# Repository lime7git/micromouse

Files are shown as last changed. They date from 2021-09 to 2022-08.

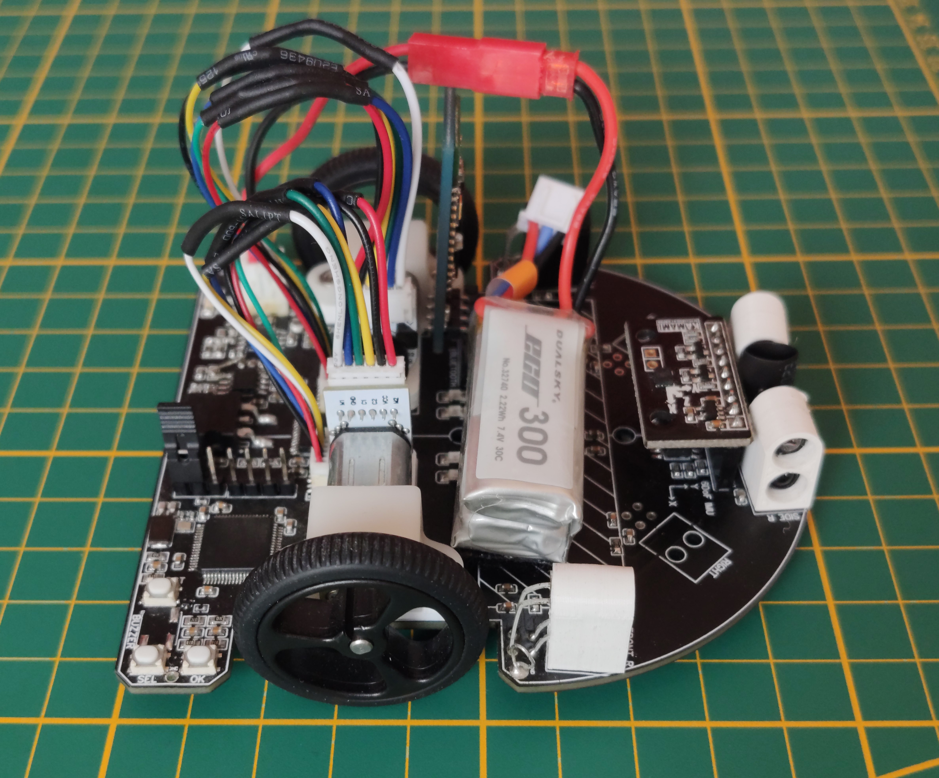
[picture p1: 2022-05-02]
micromouse-hardware/image8.jpg

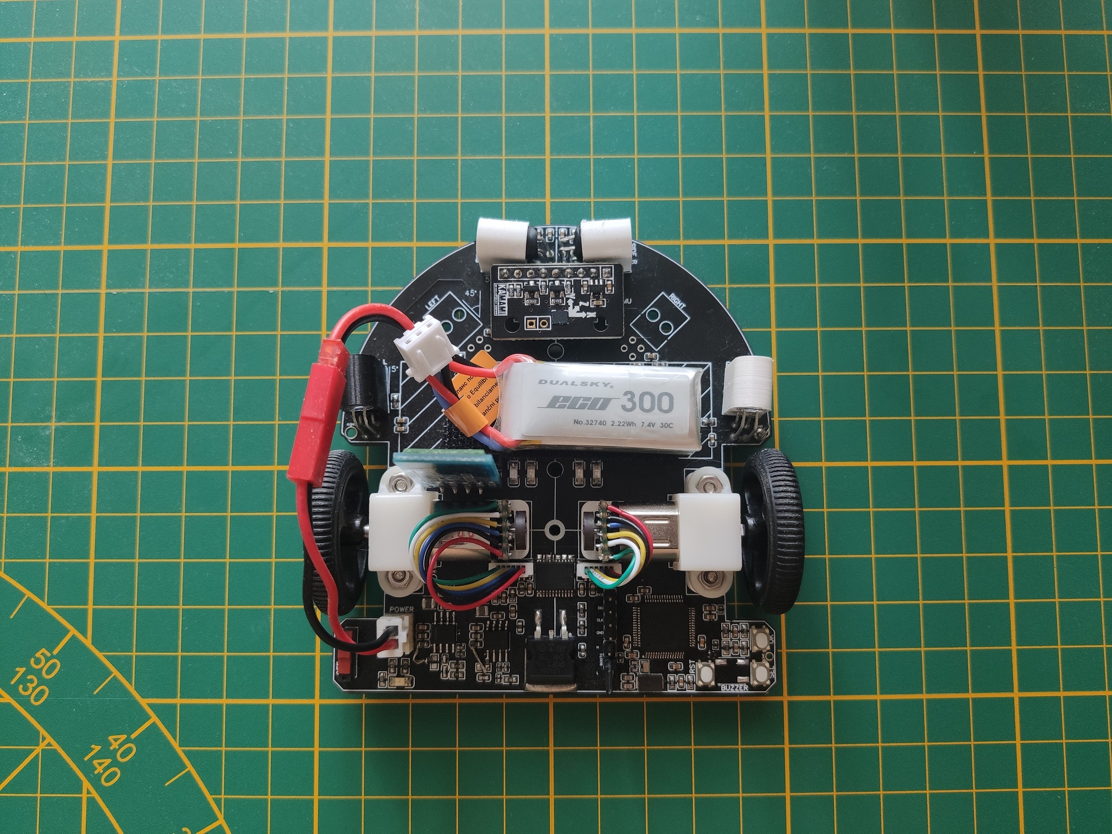
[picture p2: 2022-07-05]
micromouse-hardware/image12.jpg

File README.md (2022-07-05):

# micromouse

Project of a micromouse type mobile robot based on STM32 and designed PCB used as a chasis. It is my Master's Degree thesis at The Kielce University of Technology.

Project involve robot hardware and software design, build a small maze where robot will be tested and program a maze simulator windows application to test and compare different maze search alghoritms. The simulator is created with Qt 6 libary and Qt Creator IDE. Hardware design was created with EasyEDA. Robot's software was written in C programming language in Keil uVision5 IDE.




Maze simulator (https://youtu.be/YN4h0kgOSEQ "Micromouse")

Micromouse (https://www.youtube.com/watch?v=JYLGGba1-mw "Micromouse")

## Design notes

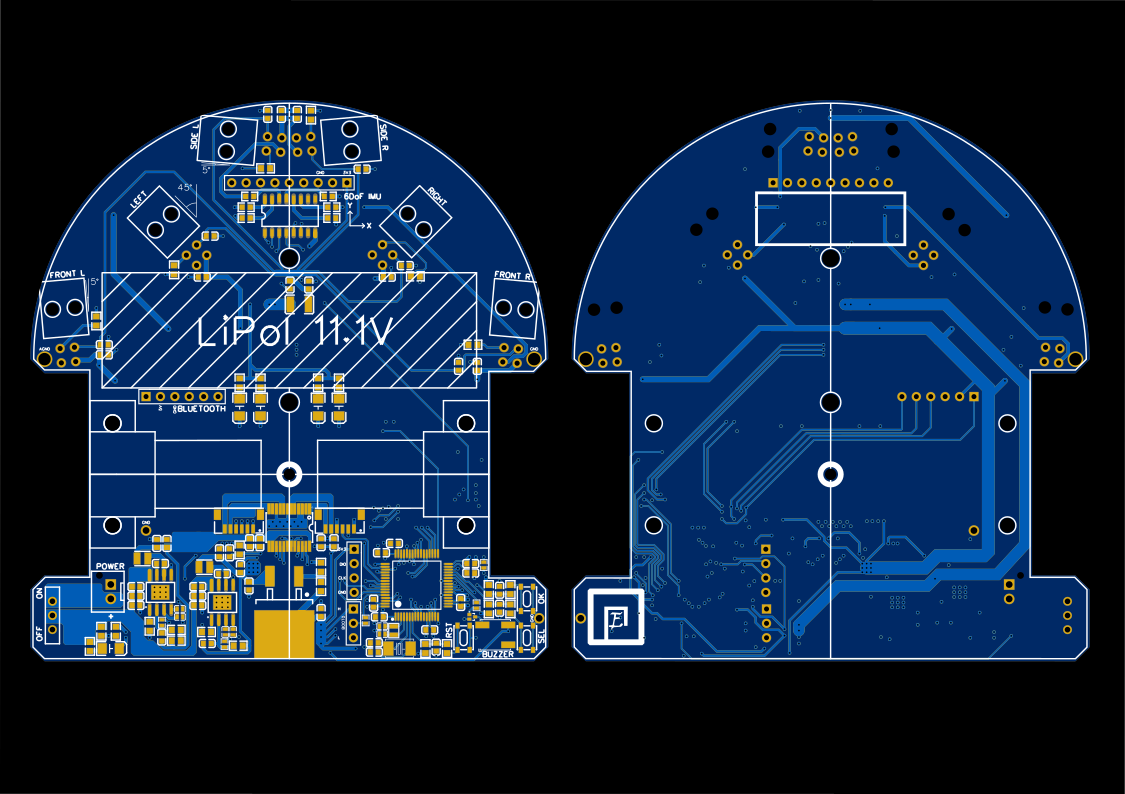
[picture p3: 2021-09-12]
micromouse-hardware/pcb-preview.png

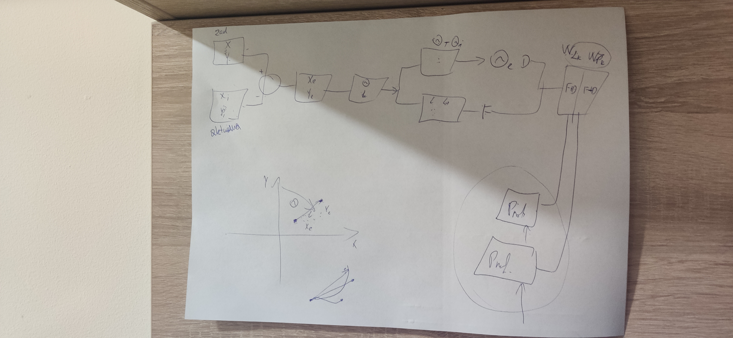
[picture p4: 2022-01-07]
micromouse-docs/position-speed-control-diagram.jpg

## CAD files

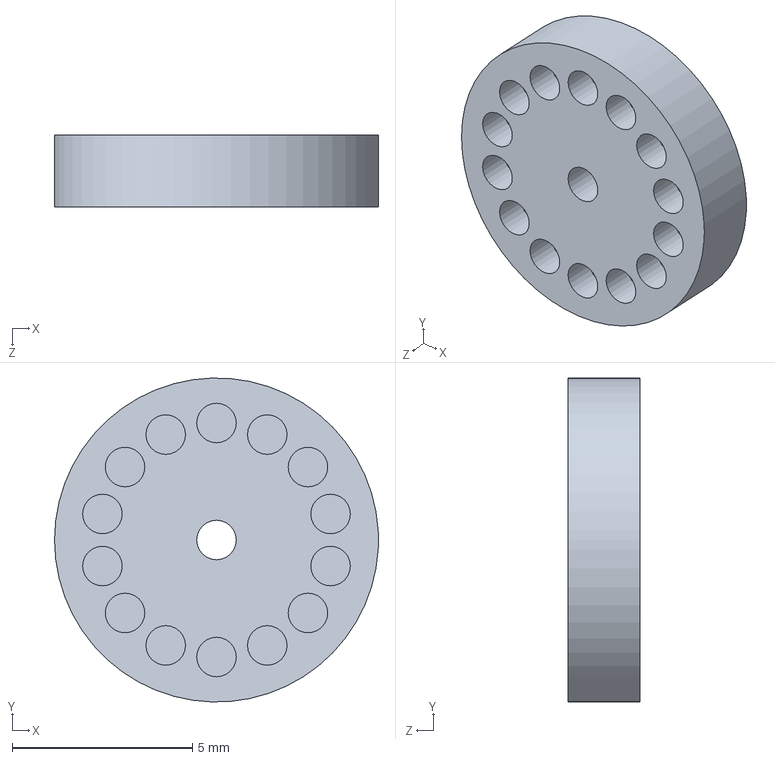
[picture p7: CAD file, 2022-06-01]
micromouse-other/encoder-magnet-disc-3d/14-pole-encoder-disk-2mm-height.SLDPRT
9.00 x 9.00 x 2.00 mm

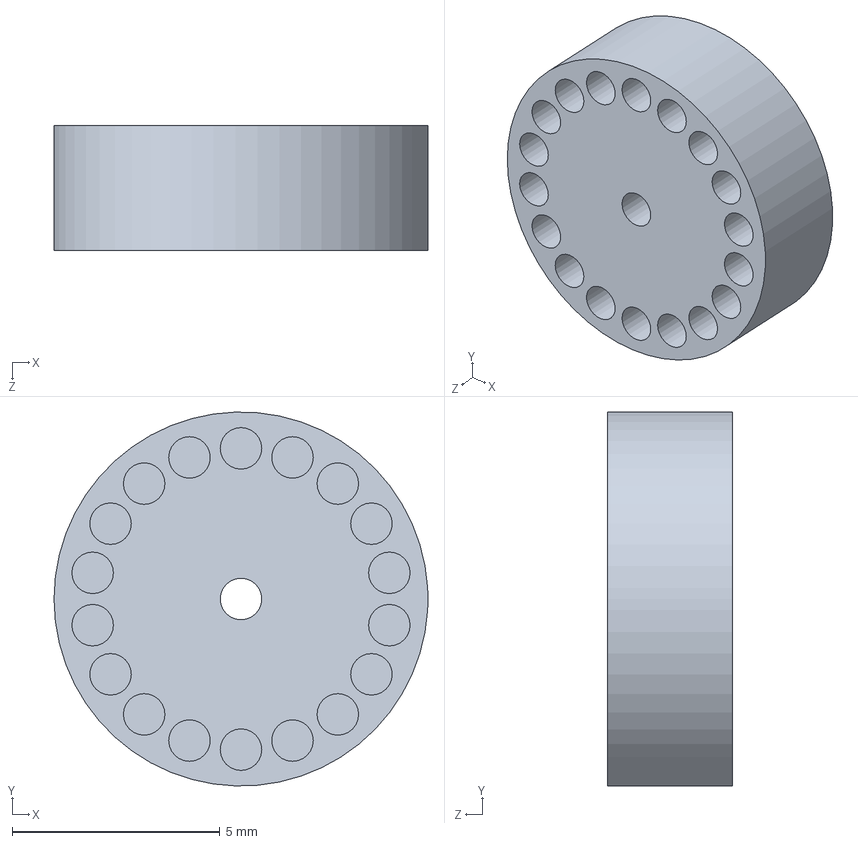
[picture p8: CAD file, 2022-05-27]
micromouse-other/encoder-magnet-disc-3d/18-pole-encoder-disk.SLDPRT
9.00 x 9.00 x 3.00 mm

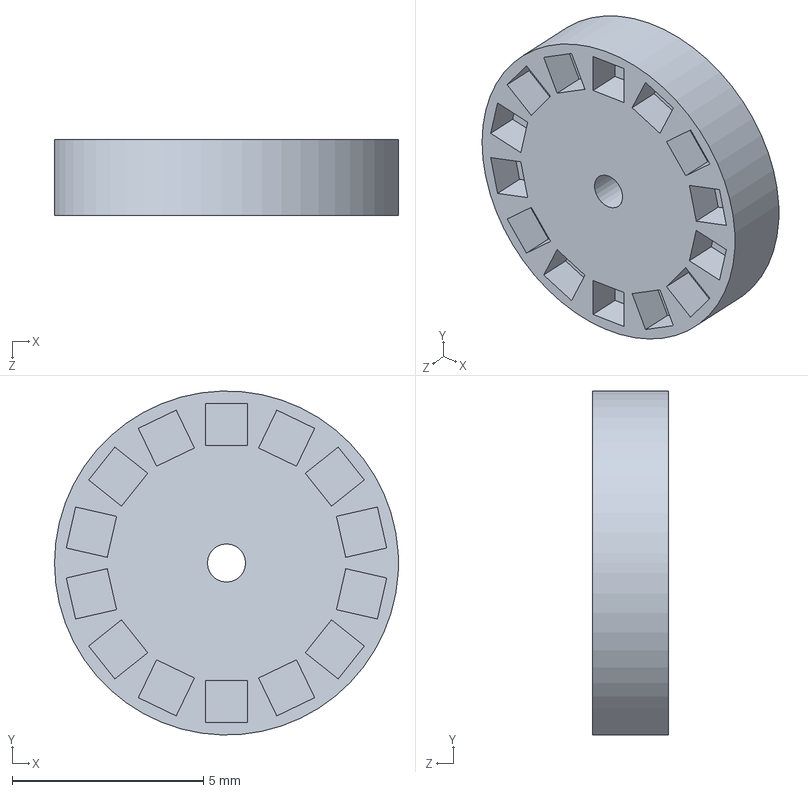
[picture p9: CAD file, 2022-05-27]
micromouse-other/encoder-magnet-disc-3d/14-pole-encoder-disk-2mm-height-square-holes.SLDPRT
9.00 x 9.00 x 2.00 mm

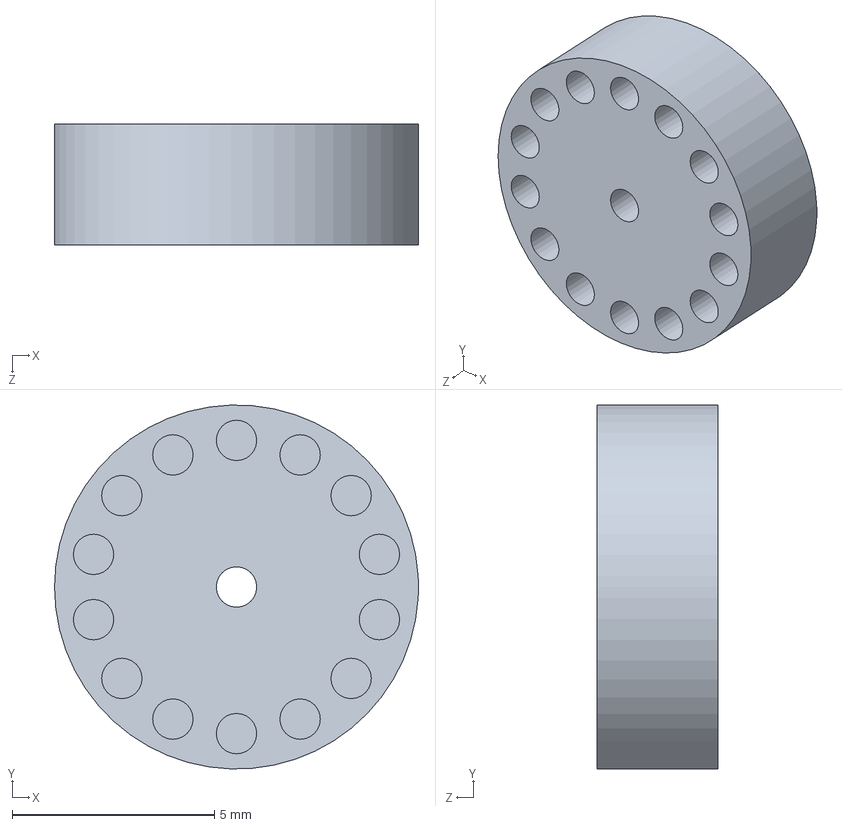
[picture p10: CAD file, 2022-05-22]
micromouse-other/encoder-magnet-disc-3d/14-pole-encoder-disk.SLDPRT
9.00 x 9.00 x 3.00 mm

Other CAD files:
micromouse-other/encoder-magnet-disc-3d/18-pole-encoder-disk-2mm-height.SLDPRT
micromouse-other/encoder-magnet-disc-3d/14-pole-encoder-disk-2mm-height-square-holes.STL
micromouse-other/encoder-magnet-disc-3d/14-pole-encoder-disk-2mm-height.STL
micromouse-other/encoder-magnet-disc-3d/14-pole-encoder-disk.STL
micromouse-other/encoder-magnet-disc-3d/18-pole-encoder-disk-2mm-height.STL
micromouse-other/encoder-magnet-disc-3d/18-pole-encoder-disk.STL

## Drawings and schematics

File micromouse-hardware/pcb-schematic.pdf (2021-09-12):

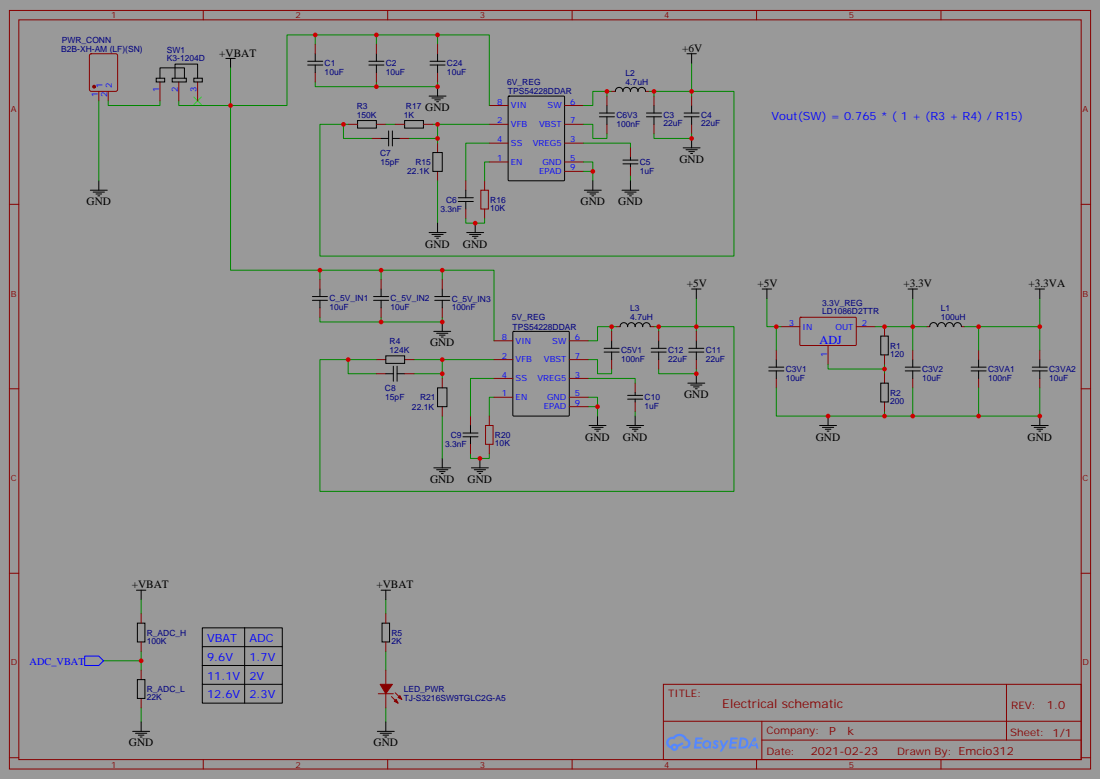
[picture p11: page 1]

PWR_CONN

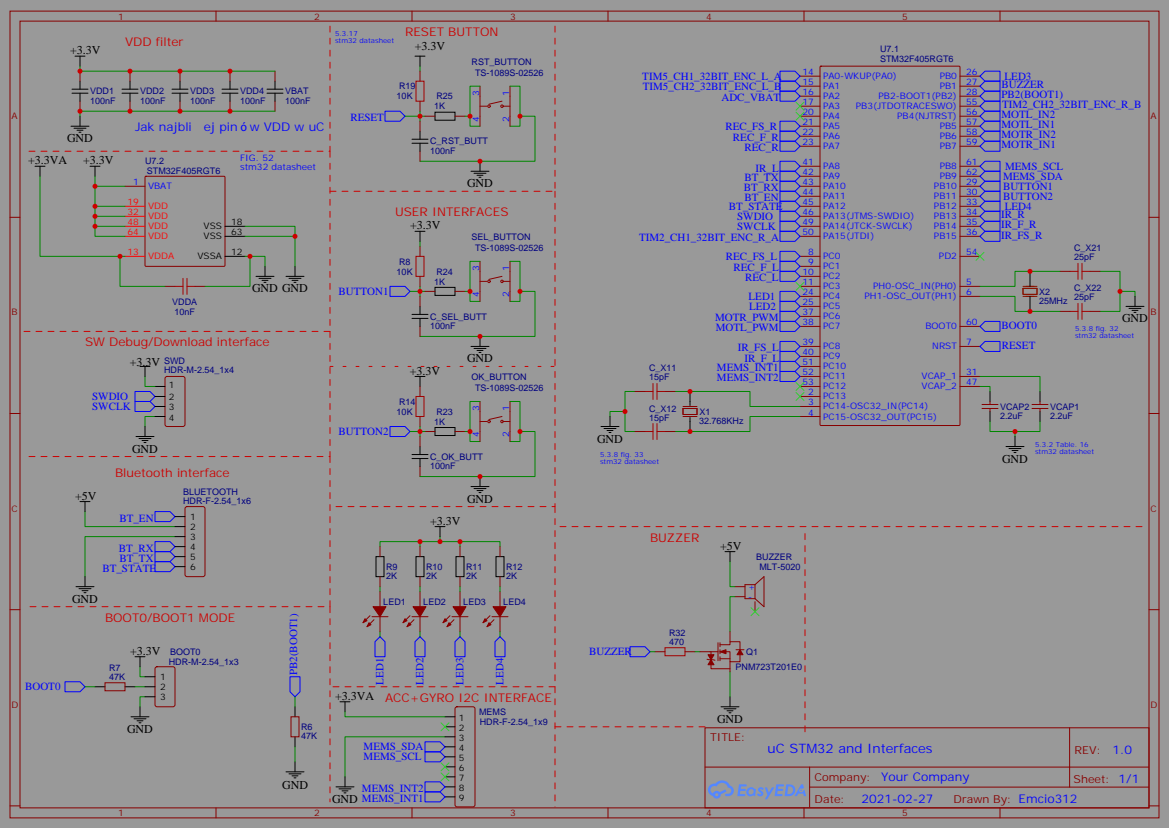
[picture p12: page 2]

VDD2
Jak najbli ej pin w VDD w uC

SW Debug/Download interface

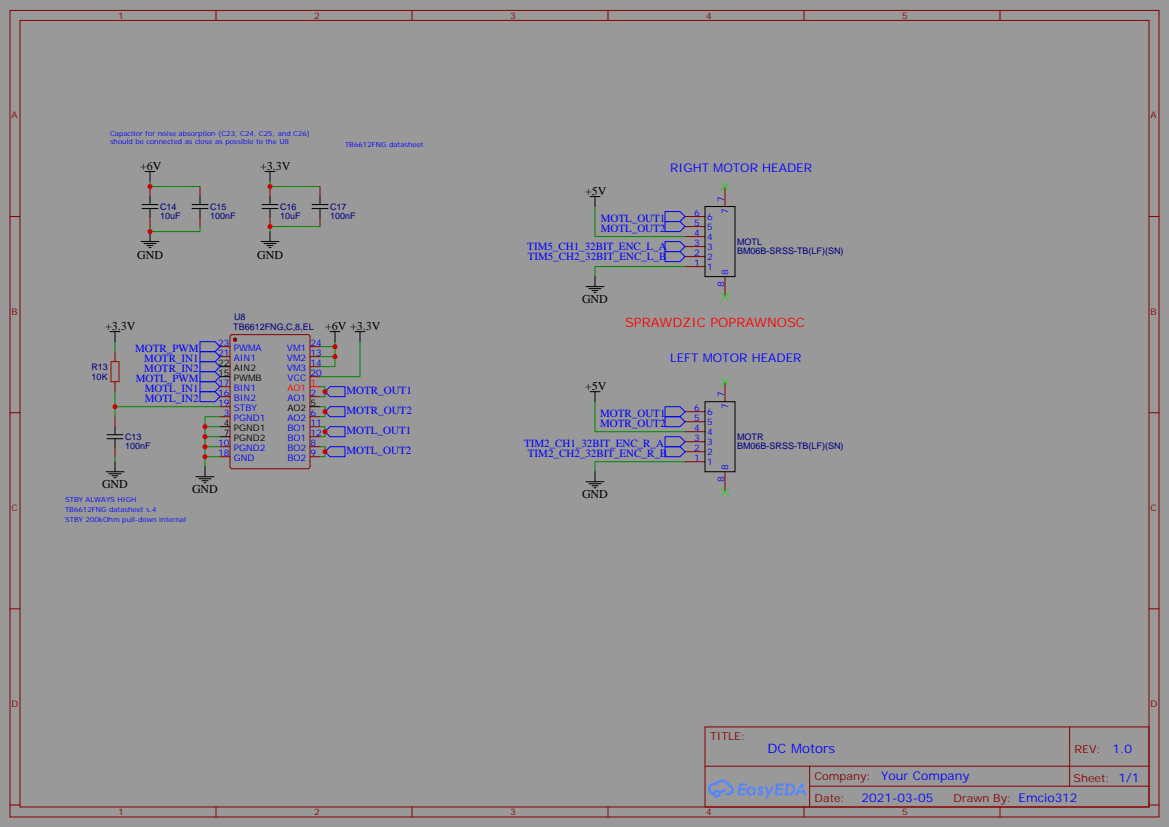
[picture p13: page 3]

Capacitor for noise absorption (C23, C24, C25, and C26)
should be connected as close as possible to the U8

STBY ALWAYS HIGH
TB6612FNG datasheet s.4
STBY 200kOhm pull-down internal

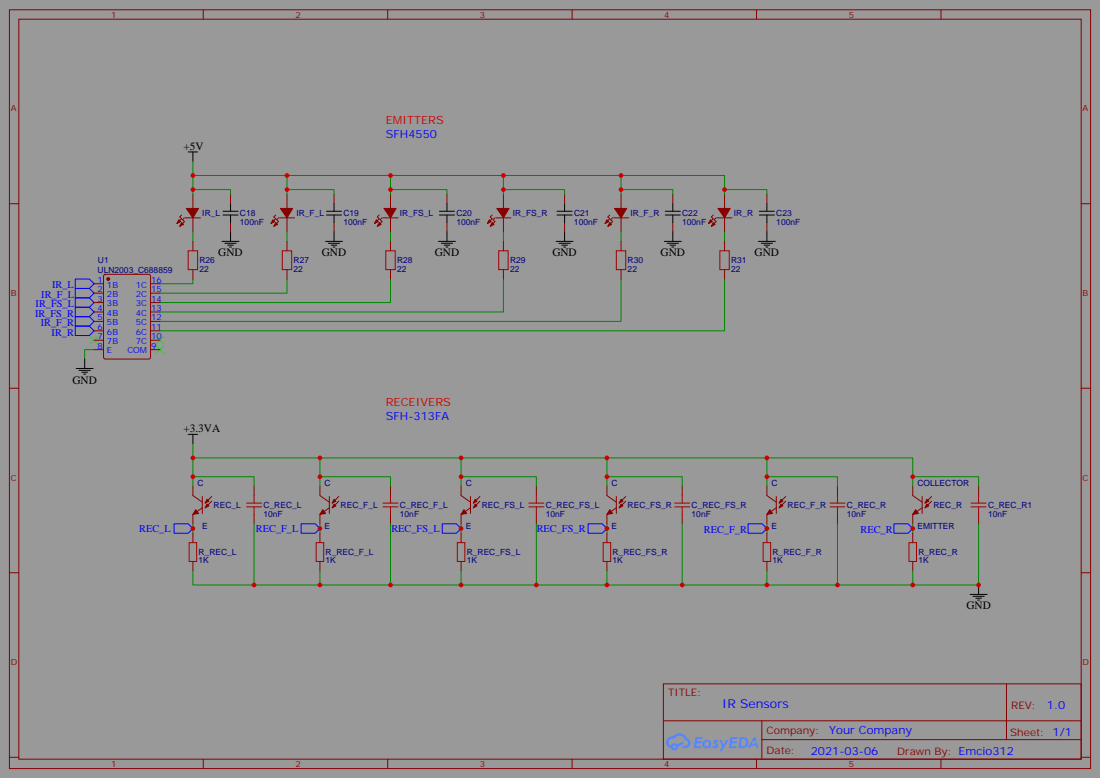
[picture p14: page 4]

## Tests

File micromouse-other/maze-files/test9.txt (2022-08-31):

0;0;9
1;0;1
2;0;1
3;0;1
4;0;1
5;0;1
6;0;1
7;0;1
8;0;1
9;0;1
10;0;1
11;0;1
12;0;1
13;0;1
14;0;1
15;0;3
0;1;8
1;1;0
2;1;0
3;1;0
4;1;0
5;1;0
6;1;0
7;1;0
8;1;0
9;1;0
10;1;0
11;1;0
12;1;0
13;1;0
14;1;0
15;1;2
0;2;8
1;2;0
2;2;0
3;2;0
4;2;0
5;2;0
6;2;4
7;2;0
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

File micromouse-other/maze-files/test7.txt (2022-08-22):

0;0;4
1;0;4
2;0;2
3;0;8
4;0;0
5;0;0
6;0;4
7;0;4
8;0;4
9;0;4
10;0;0
11;0;0
12;0;2
13;0;8
14;0;4
15;0;4
0;1;5
1;1;5
2;1;0
3;1;6
4;1;10
5;1;10
6;1;9
7;1;1
8;1;5
9;1;3
10;1;10
11;1;10
12;1;12
13;1;0
14;1;5
15;1;5
0;2;5
1;2;1
2;2;4
3;2;5
4;2;6
5;2;10
6;2;10
7;2;10
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

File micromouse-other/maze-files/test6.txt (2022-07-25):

0;0;9
1;0;1
2;0;1
3;0;1
4;0;1
5;0;3
6;0;15
7;0;13
8;0;1
9;0;1
10;0;1
11;0;5
12;0;5
13;0;5
14;0;5
15;0;7
0;1;8
1;1;0
2;1;0
3;1;0
4;1;0
5;1;0
6;1;3
7;1;15
8;1;12
9;1;0
10;1;2
11;1;13
12;1;5
13;1;5
14;1;5
15;1;7
0;2;8
1;2;0
2;2;0
3;2;0
4;2;0
5;2;0
6;2;0
7;2;3
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

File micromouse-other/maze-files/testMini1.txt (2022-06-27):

0;0;9
1;0;1
2;0;1
3;0;1
4;0;1
5;0;1
6;0;1
7;0;1
8;0;1
9;0;3
10;0;11
11;0;11
12;0;9
13;0;5
14;0;1
15;0;7
0;1;8
1;1;0
2;1;0
3;1;0
4;1;0
5;1;0
6;1;0
7;1;0
8;1;0
9;1;2
10;1;8
11;1;6
12;1;12
13;1;1
14;1;0
15;1;3
0;2;8
1;2;0
2;2;0
3;2;0
4;2;0
5;2;0
6;2;0
7;2;0
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

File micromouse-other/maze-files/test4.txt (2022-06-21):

0;0;0
1;0;0
2;0;0
3;0;0
4;0;0
5;0;0
6;0;0
7;0;0
8;0;0
9;0;0
10;0;0
11;0;4
12;0;0
13;0;0
14;0;0
15;0;0
0;1;0
1;1;0
2;1;0
3;1;0
4;1;4
5;1;4
6;1;4
7;1;4
8;1;0
9;1;0
10;1;2
11;1;11
12;1;8
13;1;0
14;1;0
15;1;0
0;2;0
1;2;0
2;2;0
3;2;2
4;2;9
5;2;1
6;2;1
7;2;3
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

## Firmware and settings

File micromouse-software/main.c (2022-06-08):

#include "uart.h"
#include "gpio.h"
#include "clock.h"
#include "adc.h"
#include "ui.h"
#include "motors.h"
#include "circular_buffer.h"
#include "encoders.h"
#include "pid.h"
#include "controller.h"
#include "timer.h"
#include "map.h"

bool flag_sensors = false;
bool flag_sensors_in_progress = false;

int main(void)
{
	tCircular_buffer_init(&UART_Buffer, 128);
	
	CLOCK_Init();
	GPIO_Init();
	ADC1_DMA_Init();
	ADC2_DMA_init();
	MOTORS_Init();
	ENCODERS_Init();
	BUTTON_EXTI_Init();
	UART1_IT_Init();
	TIM7_1KHz_INTERRUPT_Init();
	TIM9_1MHz_INTERRUPT_INIT();
	
	MOTOR_PID_INIT(&MOTOR_LEFT,  LEFT_MOTOR, 0.021f, 0.08f, 0.0003f);
	MOTOR_PID_INIT(&MOTOR_RIGHT, RIGHT_MOTOR, 0.021f, 0.08f, 0.0003f);

	MOTOR_PID_DISABLE(&MOTOR_LEFT);
	MOTOR_PID_DISABLE(&MOTOR_RIGHT);
	MOVE_CONTROLLER_DISABLE(&MOUSE);
	
	MAP_INIT(&MOUSE);
	
	MOUSE.face_direction = NORTH;
	MOUSE.state = MOUSE_IDLE;
	
	TEST_PIN2_OFF;
	TEST_PIN_OFF;
	
		
	while(1)
	{	
		
		if(flag_sensors)
		{
			TEST_PIN2_ON;
		flag_sensors_in_progress = true;	
			
		MOUSE.left_front_sensor_mm 	= SENSOR_GET_LEFT_FRONT_DISTANCE(MM);
		MOUSE.right_side_sensor_mm 	= SENSOR_GET_RIGHT_SIDE_DISTANCE(MM);
		MOUSE.left_side_sensor_mm 	= SENSOR_GET_LEFT_SIDE_DISTANCE(MM);
		MOUSE.right_front_sensor_mm = SENSOR_GET_RIGHT_FRONT_DISTANCE(MM);
			
		flag_sensors = false;
		flag_sensors_in_progress = false;
			TEST_PIN2_OFF;
		}
	
	
		STATE_Handle(); 
		UART1_COMMAND_PARSERHandler(&UART_Buffer);
		ADC_BATTERY_VOLTAGE_UPDATE();
		LED_SYSTEM_UPDATE();


		if(BUTTON_OK.wasPressed && SHORT_PRESS(BUTTON_OK.time))
		{
			delay_ms(1000);
			MOVE_CELL_FORWARD(&MOUSE, 1);
		
			BUTTON_OK.wasPressed = false;
		}	

		if(BUTTON_OK.wasPressed && NORMAL_PRESS(BUTTON_OK.time))
		{
			delay_ms(1000);
			MOVE_SET_ORIENTATION(&MOUSE, 90.0f);
				
			BUTTON_OK.wasPressed = false;
		}	
		
		if(BUTTON_OK.wasPressed && LONG_PRESS(BUTTON_OK.time))
		{
			delay_ms(1000);
			MOVE_SET_ORIENTATION(&MOUSE, 180.0f);
				
			BUTTON_OK.wasPressed = false;
		}	
			
		if(BUTTON_SEL.wasPressed && LONG_PRESS(BUTTON_SEL.time))
		{
			STATE_Selection();
				
			BUTTON_SEL.wasPressed = false;
		}
	}
}

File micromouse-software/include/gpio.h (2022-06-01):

#ifndef _GPIO_H
#define _GPIO_H

#include "stm32f405xx.h"
#include "stm32f4xx.h"
#include "stdbool.h"

#define LED1_TOG		GPIOC->ODR ^= GPIO_ODR_OD4
#define LED1_ON 		GPIOC->ODR &= ~GPIO_ODR_OD4
#define LED1_OFF 		GPIOC->ODR |= GPIO_ODR_OD4

#define LED2_TOG		GPIOC->ODR ^= GPIO_ODR_OD5
#define LED2_ON 		GPIOC->ODR &= ~GPIO_ODR_OD5
#define LED2_OFF 		GPIOC->ODR |= GPIO_ODR_OD5

#define LED3_TOG		GPIOB->ODR ^= GPIO_ODR_OD0
#define LED3_ON 		GPIOB->ODR &= ~GPIO_ODR_OD0
#define LED3_OFF 		GPIOB->ODR |= GPIO_ODR_OD0

#define LED4_TOG		GPIOB->ODR ^= GPIO_ODR_OD12
#define LED4_ON 		GPIOB->ODR &= ~GPIO_ODR_OD12
#define LED4_OFF 		GPIOB->ODR |= GPIO_ODR_OD12

#define IR_LEFT_FRONT_ON 			GPIOA->ODR |= GPIO_ODR_OD8
#define IR_LEFT_FRONT_OFF 		GPIOA->ODR &= ~GPIO_ODR_OD8

#define IR_RIGHT_FRONT_ON 		GPIOB->ODR |= GPIO_ODR_OD13
#define IR_RIGHT_FRONT_OFF 		GPIOB->ODR &= ~GPIO_ODR_OD13

#define IR_LEFT_SIDE_ON				GPIOC->ODR |= GPIO_ODR_OD8
#define IR_LEFT_SIDE_OFF 			GPIOC->ODR &= ~GPIO_ODR_OD8

#define IR_RIGHT_SIDE_ON 			GPIOB->ODR |= GPIO_ODR_OD15
#define IR_RIGHT_SIDE_OFF 		GPIOB->ODR &= ~GPIO_ODR_OD15

#define TEST_PIN_ON 			GPIOB->ODR |= GPIO_ODR_OD9
#define TEST_PIN_OFF 			GPIOB->ODR &= ~GPIO_ODR_OD9

#define TEST_PIN2_ON 			GPIOB->ODR |= GPIO_ODR_OD8
#define TEST_PIN2_OFF 		GPIOB->ODR &= ~GPIO_ODR_OD8


#define IR_ALL_OFF		\
	IR_LEFT_FRONT_OFF;	\
	IR_RIGHT_FRONT_OFF; \
	IR_LEFT_SIDE_OFF; 	\
	IR_RIGHT_SIDE_OFF; 

typedef enum{LED1 = 0, LED2 = 1, LED3 = 2, LED4 = 3, LED_ALL = 4}eLEDnum;
typedef enum{OFF = 0, ON = 1, TOG = 2}eLEDstate;

void GPIO_Init(void);

typedef struct {
	bool isPressed;
	bool wasPressed;
	uint16_t time; // [ms]
}BUTTONS;

extern volatile BUTTONS BUTTON_OK;
extern volatile BUTTONS BUTTON_SEL;

#define CNT_2_MILISECONDS(value) (uint16_t)(value / 1.5f)

#define SHORT_PRESS(value) (value > 25 && value < 250)
#define NORMAL_PRESS(value) (value > 250 && value < 1500)
#define LONG_PRESS(value) (value > 1500)

void BUTTON_EXTI_Init(void);
void EXTI15_10_IRQHandler(void);

void LED_Switch(eLEDnum num, eLEDstate state);

#endif

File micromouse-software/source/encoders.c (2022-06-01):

#include "encoders.h"

void ENCODERS_Init(void)
{
	// enable clock for port A, B and enable TIM2 and TIM5
	RCC->AHB1ENR |= RCC_AHB1ENR_GPIOAEN;
	RCC->AHB1ENR |= RCC_AHB1ENR_GPIOBEN;
	RCC->APB1ENR |= RCC_APB1ENR_TIM5EN;
	RCC->APB1ENR |= RCC_APB1ENR_TIM2EN;
	
	// GPIO alternative functions
	GPIOA->MODER &= ~GPIO_MODER_MODER0;
	GPIOA->MODER |= GPIO_MODER_MODER0_1;
	GPIOA->MODER &= ~GPIO_MODER_MODER1;
	GPIOA->MODER |= GPIO_MODER_MODER1_1;
	GPIOA->AFR[0] |= 0x00000022;
	
	GPIOA->MODER &= ~GPIO_MODER_MODER15;
	GPIOA->MODER |= GPIO_MODER_MODER15_1;
	GPIOB->MODER &= ~GPIO_MODER_MODER3;
	GPIOB->MODER |= GPIO_MODER_MODER3_1;
	GPIOA->AFR[1] |= 0x10000000;
	GPIOB->AFR[0] |= 0x00001000;
	
	TIM5->PSC = 0;
	TIM5->ARR = 0xFFFFFFFF;
	
	TIM5->CCMR1 |= TIM_CCMR1_CC1S_0 | TIM_CCMR1_CC2S_0; // IC1 mapped on TI1, IC2 mapped on TI2
	TIM5->CCER 	|= (1 << TIM_CCER_CC1P_Pos) | (0 << TIM_CCER_CC2P_Pos) | (0 << TIM_CCER_CC1NP_Pos) | (0 << TIM_CCER_CC2NP_Pos) | TIM_CCER_CC1E | TIM_CCER_CC2E; // TI1 inverted, TI2 non-inverted , enable channel 1 and 2
	TIM5->SMCR 	|= TIM_SMCR_SMS_0 | TIM_SMCR_SMS_1; // encoder mode 4 edges
	TIM5->CR1 	|= TIM_CR1_CEN; // counter enable
	
	TIM2->PSC = 0;
	TIM2->ARR = 0xFFFFFFFF;
	
	TIM2->CCMR1 |= TIM_CCMR1_CC1S_0 | TIM_CCMR1_CC2S_0;
	TIM2->CCER 	|= (0 << TIM_CCER_CC1P_Pos) | (0 << TIM_CCER_CC2P_Pos) | (0 << TIM_CCER_CC1NP_Pos) | (0 << TIM_CCER_CC2NP_Pos) | TIM_CCER_CC1E | TIM_CCER_CC2E;
	TIM2->SMCR 	|= TIM_SMCR_SMS_0 | TIM_SMCR_SMS_1; // encoder mode 4 edges
	TIM2->CR1 	|= TIM_CR1_CEN;
}
int32_t ENCODER_GET_VALUE(sMOT *pMOTOR)
{
	int32_t value;
	
	switch (pMOTOR->motorSide)
	{
		case LEFT_MOTOR:
		{
			value = (int32_t)TIM5->CNT;
		break;
		}
		
		case RIGHT_MOTOR:
		{
			value = (int32_t)TIM2->CNT;
		break;
		}
	}
	
	return value;
}
void CALCULATE_ACTUAL_POSITION(sMOUSE *pMOUSE, sMOT *pMOTOR_LEFT, sMOT *pMOTOR_RIGHT)
{
	float distance;
	float actual_angle_temporary;
	
	pMOTOR_LEFT->encPrev 			= pMOTOR_LEFT->enc;
	pMOTOR_LEFT->enc 					= ENCODER_GET_VALUE(pMOTOR_LEFT);
	pMOTOR_LEFT->encDiff 			= pMOTOR_LEFT->enc - pMOTOR_LEFT->encPrev;
	pMOTOR_LEFT->dist 				= (float)pMOTOR_LEFT->encDiff / ENC_IMP_PER_ROTATE * CIRCUMFERENCE_OF_WHEEL;
	pMOTOR_LEFT->totalDist 		+= pMOTOR_LEFT->dist;
	
	pMOTOR_RIGHT->encPrev 		= pMOTOR_RIGHT->enc;
	pMOTOR_RIGHT->enc 				= ENCODER_GET_VALUE(pMOTOR_RIGHT);
	pMOTOR_RIGHT->encDiff 		= pMOTOR_RIGHT->enc - pMOTOR_RIGHT->encPrev;
	pMOTOR_RIGHT->dist 				= (float)pMOTOR_RIGHT->encDiff / ENC_IMP_PER_ROTATE * CIRCUMFERENCE_OF_WHEEL;
	pMOTOR_RIGHT->totalDist 	+= pMOTOR_RIGHT->dist;
	
	actual_angle_temporary = ((pMOTOR_LEFT->totalDist - pMOTOR_RIGHT->totalDist) * ROTATE_CALIB) / DISTANCE_BETWEEN_WHEELS * RAD_TO_DEG;
	pMOUSE->actual_angle = fmodf(actual_angle_temporary, 360.0f);
	
	if(pMOUSE->actual_angle < -180.0f)
	{
		pMOUSE->actual_angle += 360.0f;
	}
	else if(pMOUSE->actual_angle > 180.0f)
	{
		pMOUSE->actual_angle -= 360.0f;
	}

	distance = (pMOTOR_LEFT->dist + pMOTOR_RIGHT->dist) / 2.0f;
	
	pMOUSE->actual_position_x += distance * sinf(pMOUSE->actual_angle * DEG_TO_RAD);
	pMOUSE->actual_position_y += distance * cosf(pMOUSE->actual_angle * DEG_TO_RAD);
	
	pMOTOR_LEFT->act_rpm 	= ((float)pMOTOR_LEFT->encDiff 	/ TIME_STAMP * 60.0f) / ENC_IMP_PER_ROTATE;
	pMOTOR_RIGHT->act_rpm = ((float)pMOTOR_RIGHT->encDiff / TIME_STAMP * 60.0f) / ENC_IMP_PER_ROTATE;
	
	pMOTOR_LEFT->act_rpm_filtered = 0.854f * pMOTOR_LEFT->act_rpm_filtered + 0.0728f * pMOTOR_LEFT->act_rpm + 0.0728f * pMOTOR_LEFT->prev_rpm;
	pMOTOR_LEFT->prev_rpm = pMOTOR_LEFT->act_rpm;
	
	pMOTOR_RIGHT->act_rpm_filtered = 0.854f * pMOTOR_RIGHT->act_rpm_filtered + 0.0728f * pMOTOR_RIGHT->act_rpm + 0.0728f * pMOTOR_RIGHT->prev_rpm;
	pMOTOR_RIGHT->prev_rpm = pMOTOR_RIGHT->act_rpm;
	
}

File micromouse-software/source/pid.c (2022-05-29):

#include "pid.h"
#include "motors.h"

sMOT MOTOR_LEFT;
sMOT MOTOR_RIGHT;

void MOTOR_PID_INIT(sMOT *pMOTOR, eMOT motor_side, float kp, float ki, float kd)
{
	pMOTOR->motorSide = motor_side;
	pMOTOR->pidEnable = false;
	pMOTOR->kp = kp;
	pMOTOR->ki = ki;
	pMOTOR->kd = kd;
	
	pMOTOR->set_rpm = 0.0f;
	pMOTOR->act_rpm = 0.0f;
	pMOTOR->e = 0.0f;
	pMOTOR->e_prev = 0.0f;
	pMOTOR->e_total = 0.0f;
	pMOTOR->out = 0.0f;
	pMOTOR->enc = 0;
	pMOTOR->encPrev = 0;
	pMOTOR->encDiff = 0;
	pMOTOR->totalDist = 0.0f;
	pMOTOR->dist = 0.0f;
}
void MOTOR_PID_CONTROLLER(sMOT *pMOTOR)
{
	pMOTOR->e_prev = pMOTOR->e;
  pMOTOR->e = pMOTOR->set_rpm - pMOTOR->act_rpm_filtered;
	pMOTOR->e_total += pMOTOR->e;
	
	if(pMOTOR->e_total > 1750.0f)		
		pMOTOR->e_total = 1750.0f;
	else if(pMOTOR->e_total < -1750.0f)	
		pMOTOR->e_total = -1750.0f;
	
	pMOTOR->out = pMOTOR->kp * pMOTOR->e + pMOTOR->ki * pMOTOR->e_total * TIME_STAMP + pMOTOR->kd * (pMOTOR->e - pMOTOR->e_prev) / TIME_STAMP;

	if(pMOTOR->out > 1.0f) 	
		pMOTOR->out = 1.0f;
	else if(pMOTOR->out < -1.0f)	
		pMOTOR->out = -1.0f;
	
	MOTOR_SET_SPEED(pMOTOR, pMOTOR->out);
}
void MOTOR_PID_ENABLE(sMOT *pMOTOR)
{
	pMOTOR->pidEnable = true;
}
void MOTOR_PID_DISABLE(sMOT *pMOTOR)
{
	pMOTOR->pidEnable = false;
}
bool MOTOR_PID_IS_ENABLE(sMOT *pMOTOR)
{
	return pMOTOR->pidEnable;
}

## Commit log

2021-09-13 Added UART log function
2021-09-18 Positioning and motor controller
    Writed some PID and calculating position code, trying to get the same work as previous micromouse robot.
2021-09-20 PID implement
    Still need to tune pid fine
2021-09-21 Change UART commands parsing
2021-09-22 Working on UART command handling
    Added commands with multiple parameters. Frame syntax is now : $COMMAND=param1,param2,...,paramN#
    e.g. $MOTOR=50,-75# - sets left motor pwm to 50 and right motor pwm to -75
2021-09-22 Added battery command
2021-09-27 Added <READY> command to test if micromouse response properly
    When any device send command "$READY=?#" to the Micromouse - it will reply "READY\r\n"
2021-10-12 Rename and add some mouse states, updates on PID control
2021-10-27 Change microcontroller's frequency, work on PID and controller
2021-11-16 PID tuning, and work on velocity profiler
2021-12-07 Working on a velocity profiler structure
    This commit contains a lot of warnings and errors due to a lot of name changes and some other stuff
    [adc.c, adc.h, encoders.c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]
2021-12-08 Translation and rotation profiler (not working yet but i think its a small mistake), some code refactoring
    [adc.c, encoders.c, main.c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]
2022-01-08 Profiler with some problems
    [main.c, pid.c, timer.c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]
2022-01-12 Distance sensors
    Configured ADC2 with DMA2 to read phototransistors
2022-01-12 Added IR diodes
2022-04-05 added sensors
2022-04-06 Sensors update
2022-04-15 sensors software update
2022-04-16 sensors update ...
2022-04-19 matlab script for sensors curve fit
2022-04-19 Test calibrate left front sensor
2022-04-24 Sensors calbirated v.1.0
2022-04-24 Motor and encoders polarity fix
    [encoders.c, motors.h]
2022-04-25 Buzzer code temporary remove
    [adc.c, gpio.c, gpio.h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]
2022-04-25 Battery voltage measurment - added mean from 100 readings
2022-05-14 change pwm frequnecy to 14kHz, delete unnecessery operations
2022-05-22 encoder magnetic disc improvement
    [14-pole-encoder-disk.SLDPRT, 14-pole-encoder-disk.STL, 18-pole-encoder-disk.SLDPRT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]
2022-05-27 3d printed encoder discs
    [14-pole-encoder-disk-2mm-height-square-holes.SLDPRT, 14-pole-encoder-disk-2mm-height-square-holes.STL, 14-pole-encoder-disk-2mm-height.SLDPRT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]
2022-05-29 better pid
2022-05-29 act rpm low pass filter
2022-06-01 encoder discs update
    [14-pole-encoder-disk-2mm-height.SLDPRT, 14-pole-encoder-disk-2mm-height.STL]
2022-06-01 encoder reverse error fix
    [encoders.c]
2022-06-01 adc battery voltage measurment with 0.4 Hz frequency
2022-06-01 1 MHz timer for us delay
2022-06-01 ir sensor measurment sequency flag
2022-06-02 system led blinking non-blocking
2022-06-02 code refactor and battery voltage mesurments in constant time delay
2022-06-09 button test
2022-06-09 path button added
2022-06-09 flood fill counter printf
2022-06-17 flood fill fix, a* init
    [cell.h]
